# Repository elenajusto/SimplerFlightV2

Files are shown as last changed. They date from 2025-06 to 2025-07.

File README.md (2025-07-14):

# SimplerFlightV2

## Architecture
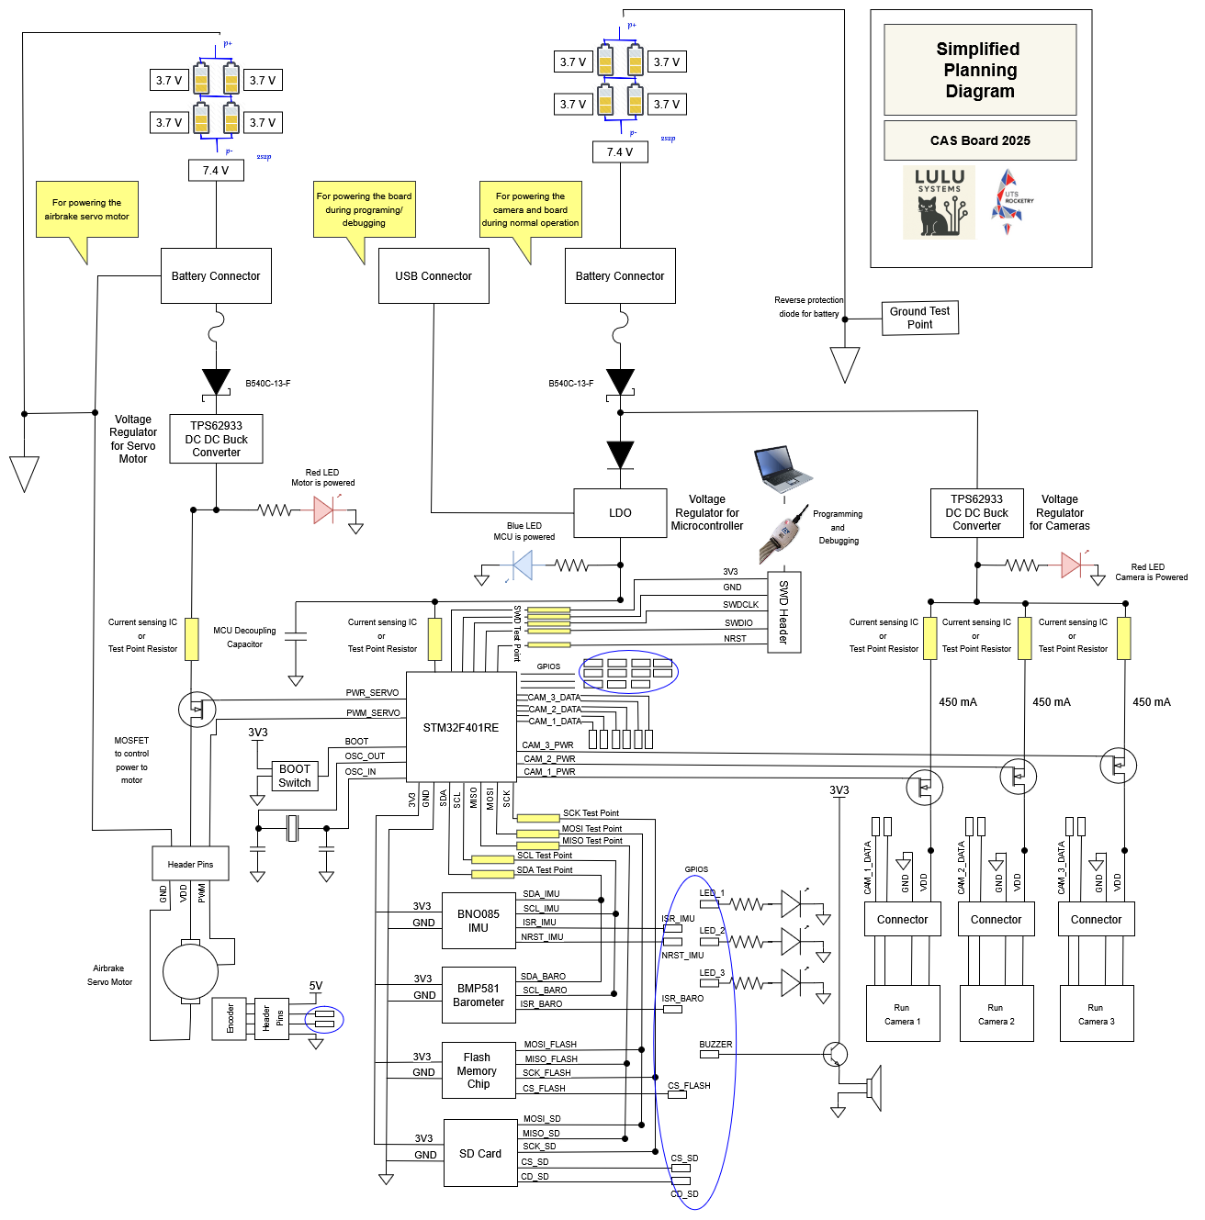
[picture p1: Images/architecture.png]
Architecture


## Simulations
Simulations done using Falstad. Available at: https://www.falstad.com/circuit/

### Buzzer
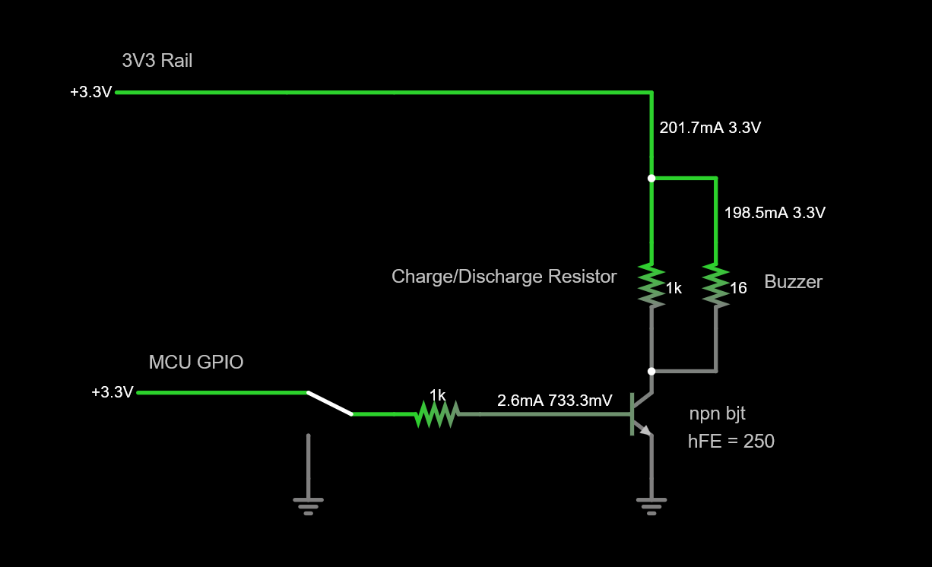
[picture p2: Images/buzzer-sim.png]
Buzzer-Sim


hFE value of 250 

As per characteristics of FSB560A NPN BJT at https://www.digikey.com/en/products/detail/onsemi/FSB560A/1049460

### Camera Power
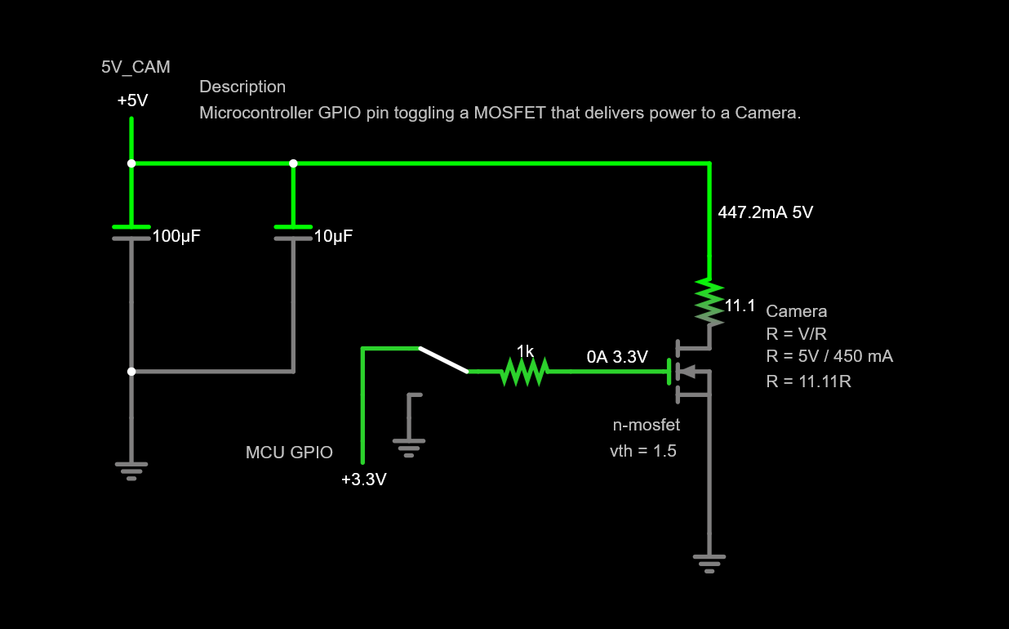
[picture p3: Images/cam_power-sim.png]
cam_power-sim-Sim


Beta value of 7.8

Assuming:
- RDS(on) (Ω) (use typical value): 0.16
- VGS where measured (V): 2.5
- Threshold (V) (use typical value): 3.3

As per characteristics of BSS816NWH6327XTSA1 N-MOSFET at https://www.digikey.com.au/en/products/detail/infineon-technologies/BSS816NWH6327XTSA1/5959970

## Microcontroller Pinout
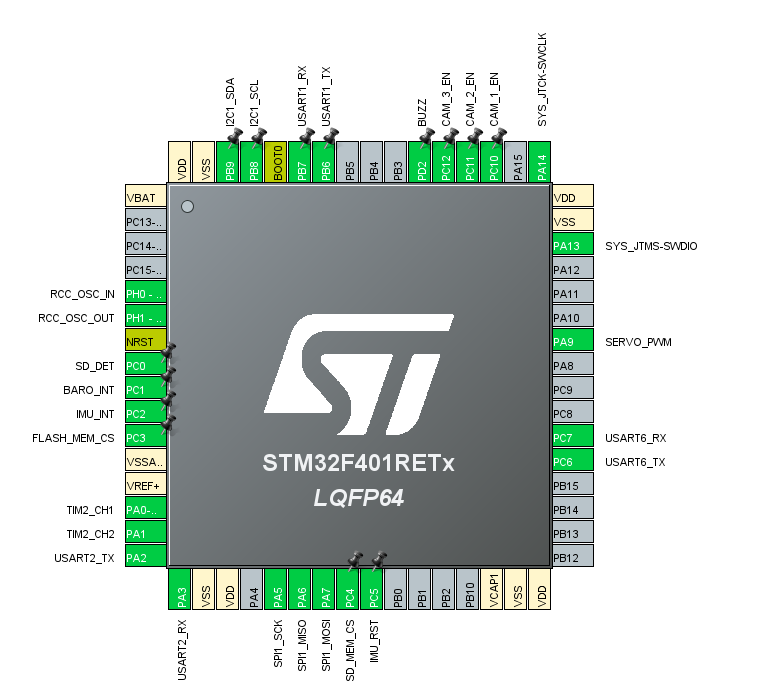
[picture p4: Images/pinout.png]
Pinout


## Schematic

### Root
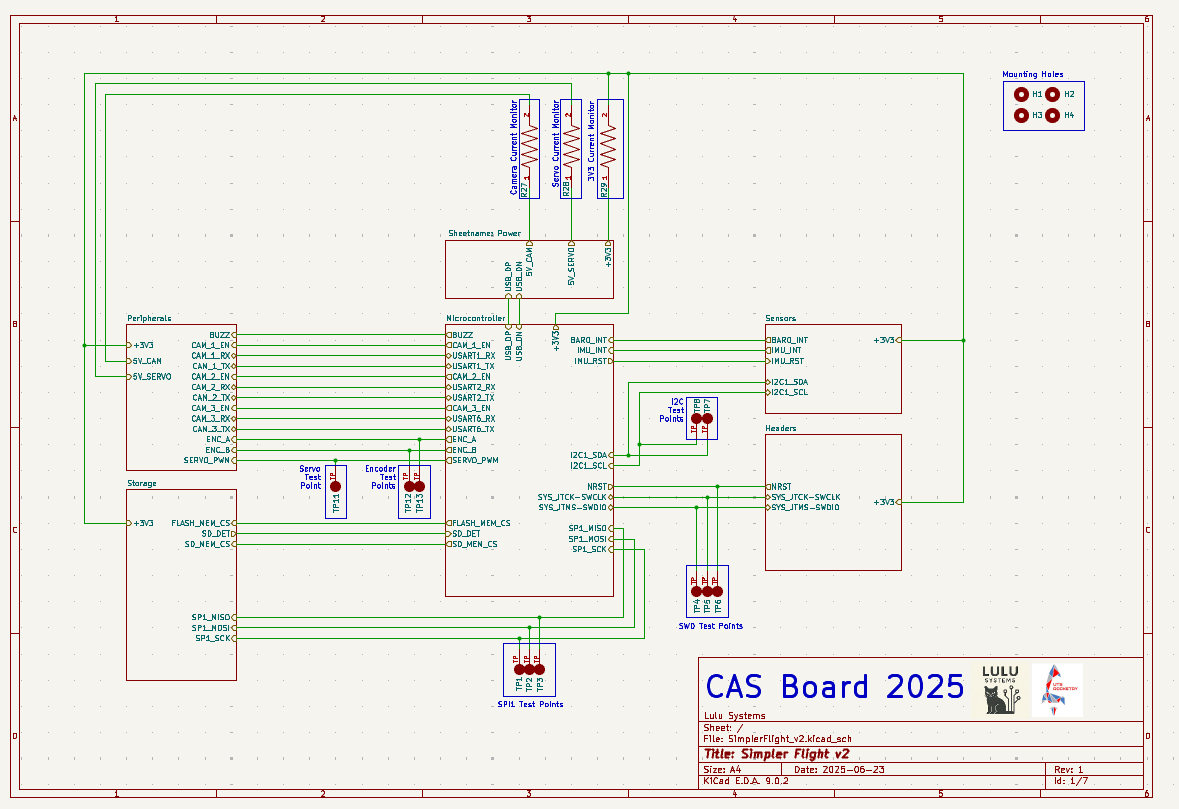
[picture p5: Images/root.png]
Root


### Microcontroller
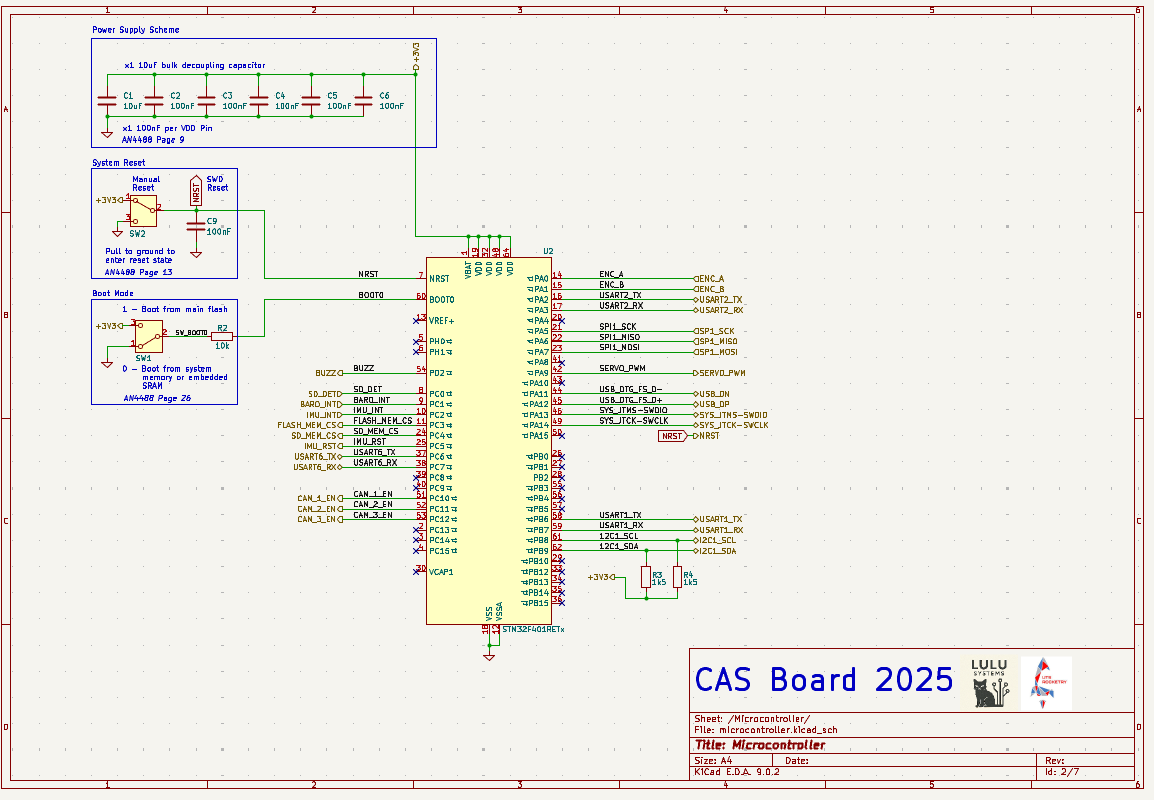
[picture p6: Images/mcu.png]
Microcontroller


### Power
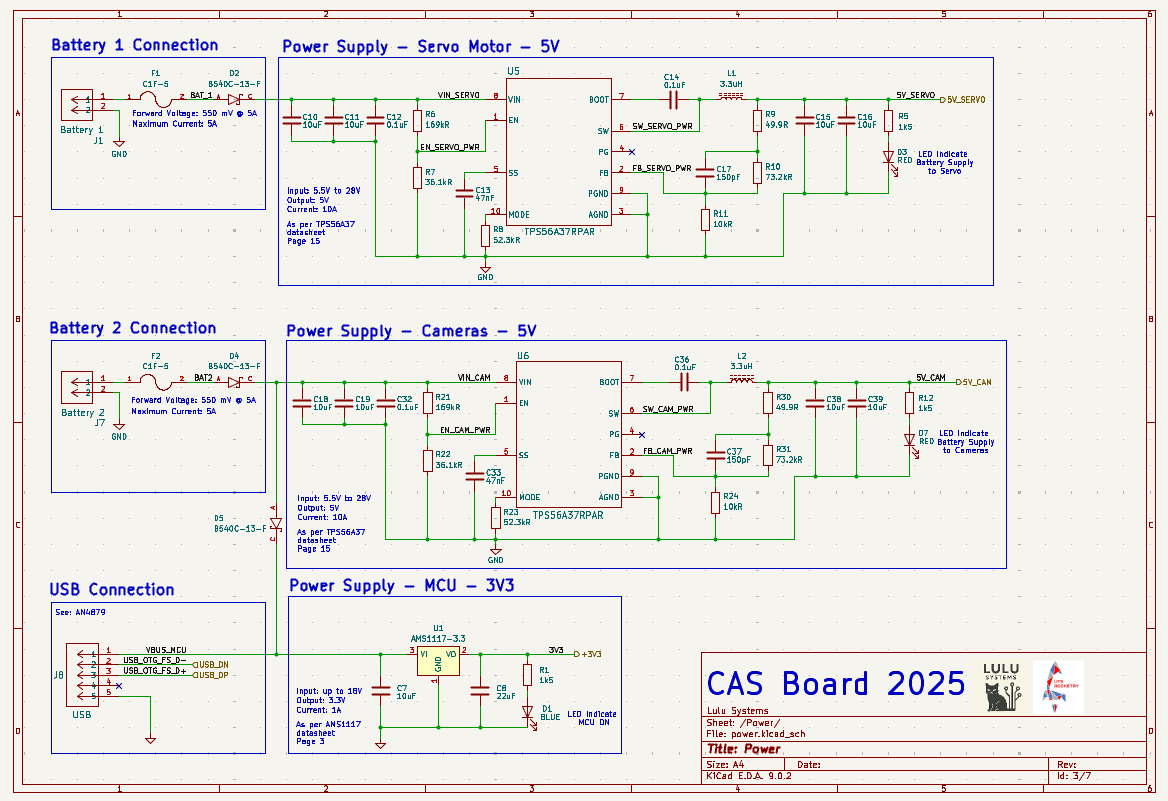
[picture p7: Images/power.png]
Power


### Sensors
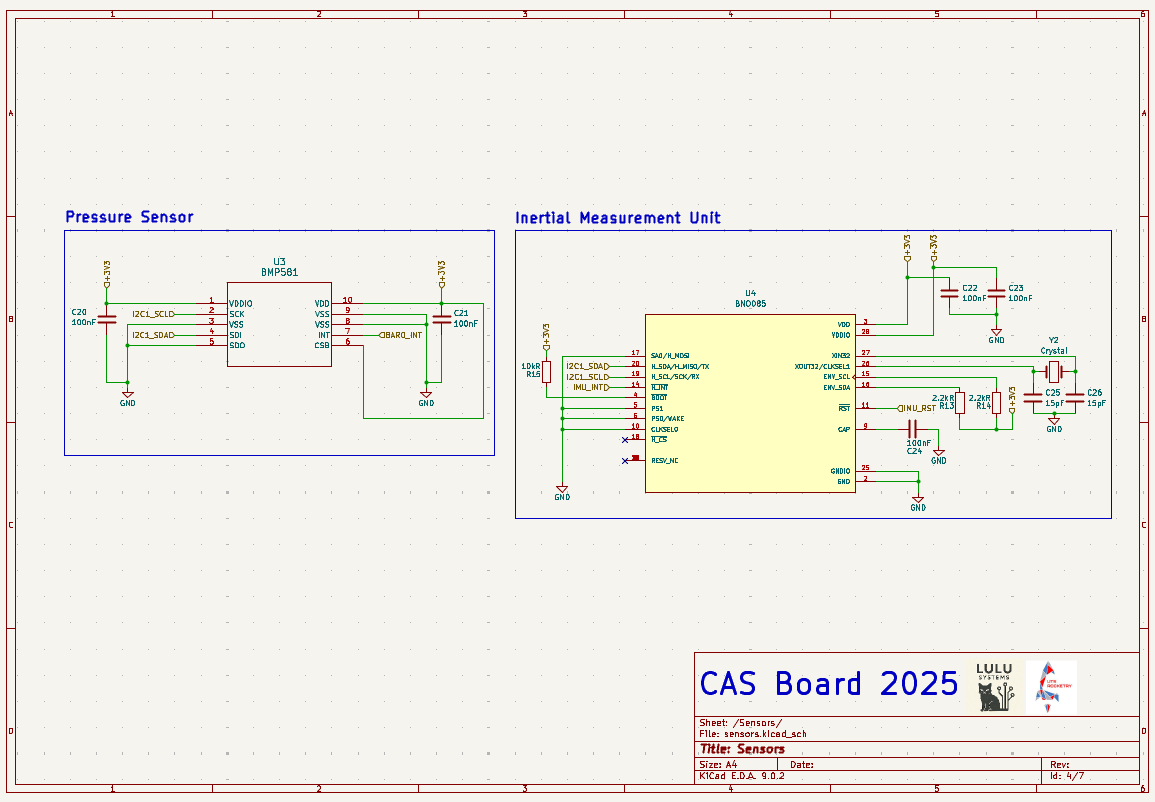
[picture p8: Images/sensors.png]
Sensors


### Storage
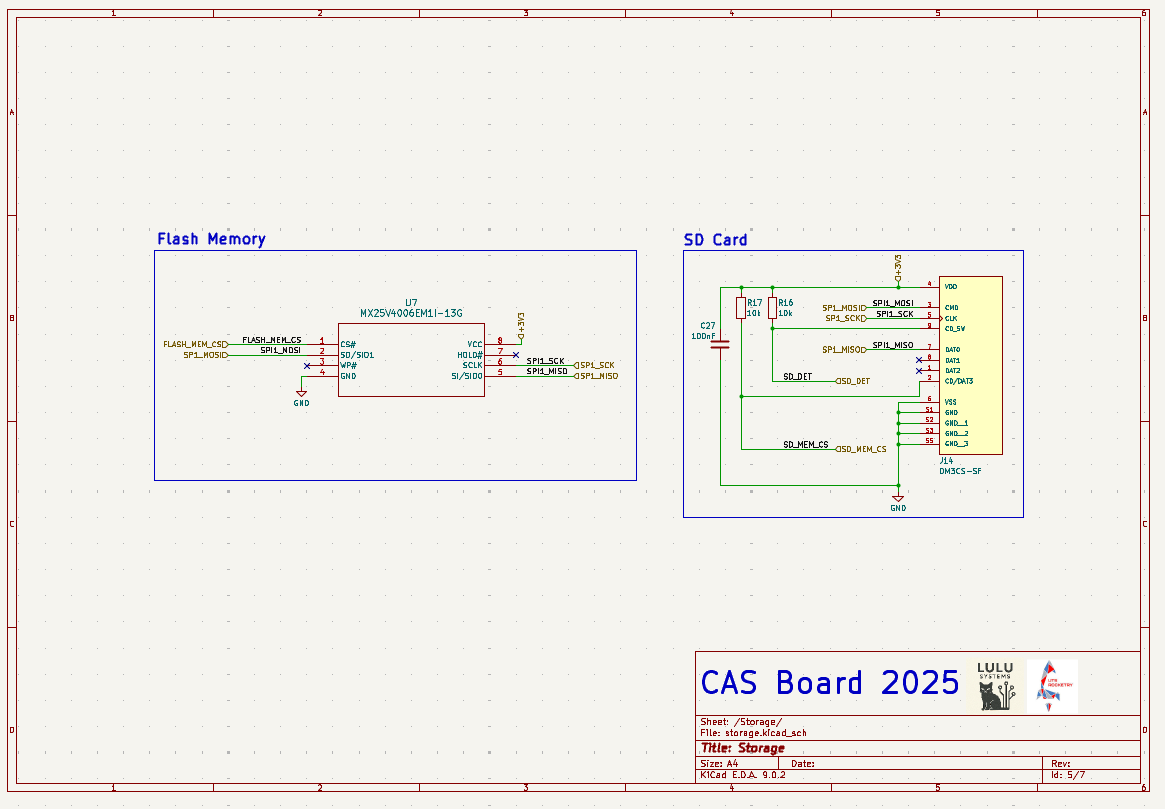
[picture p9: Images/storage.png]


### Peripherals
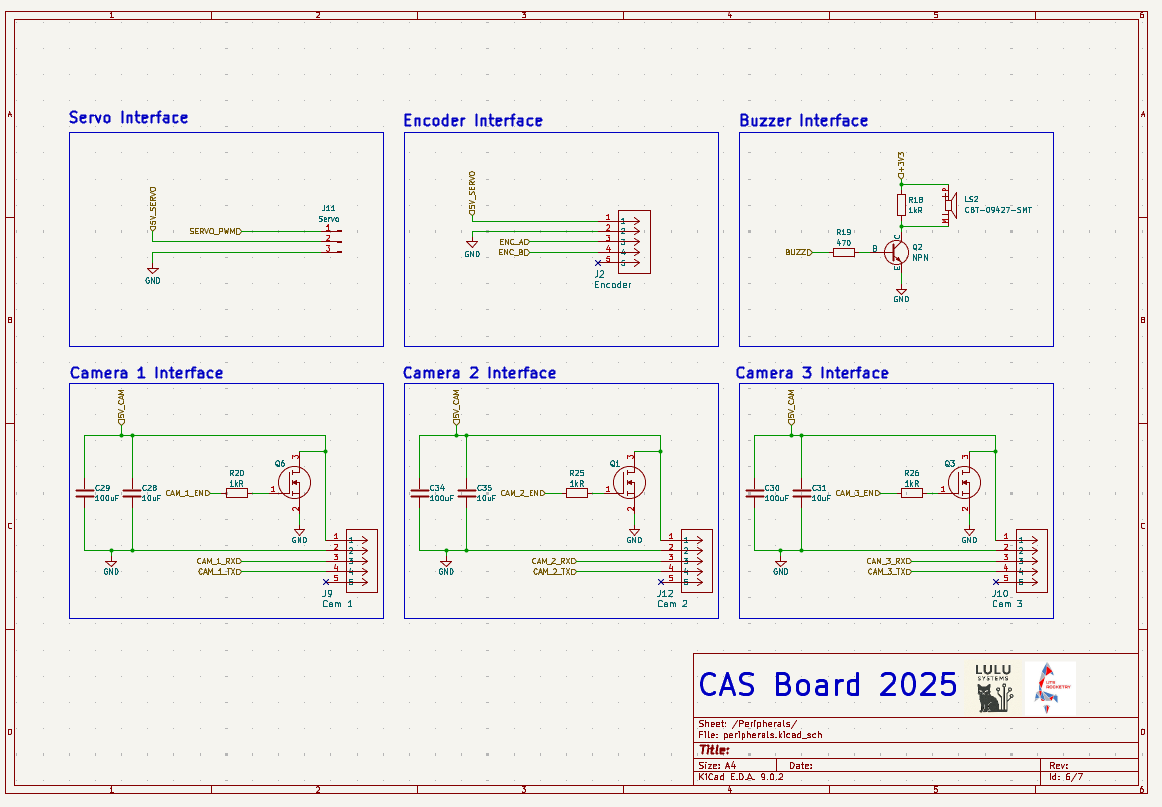
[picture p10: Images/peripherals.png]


### Headers
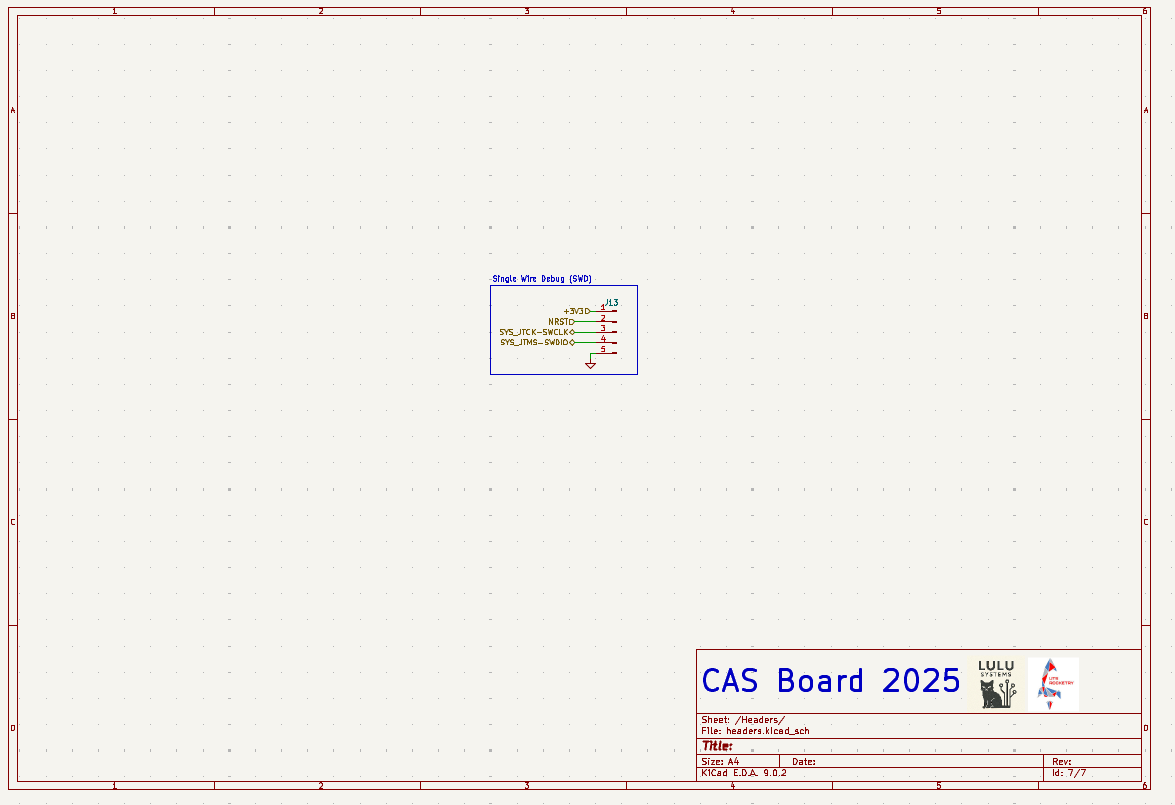
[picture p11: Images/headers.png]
Headers


## Routing
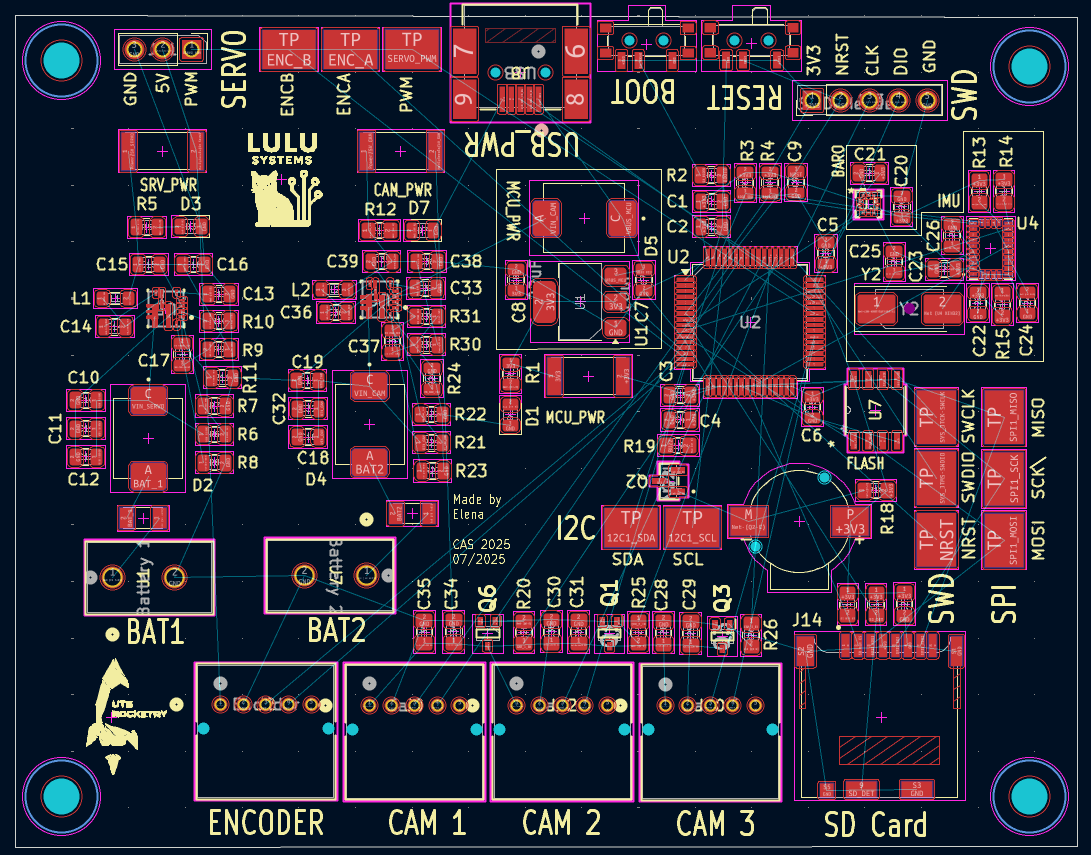
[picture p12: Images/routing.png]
Routing


## PCB
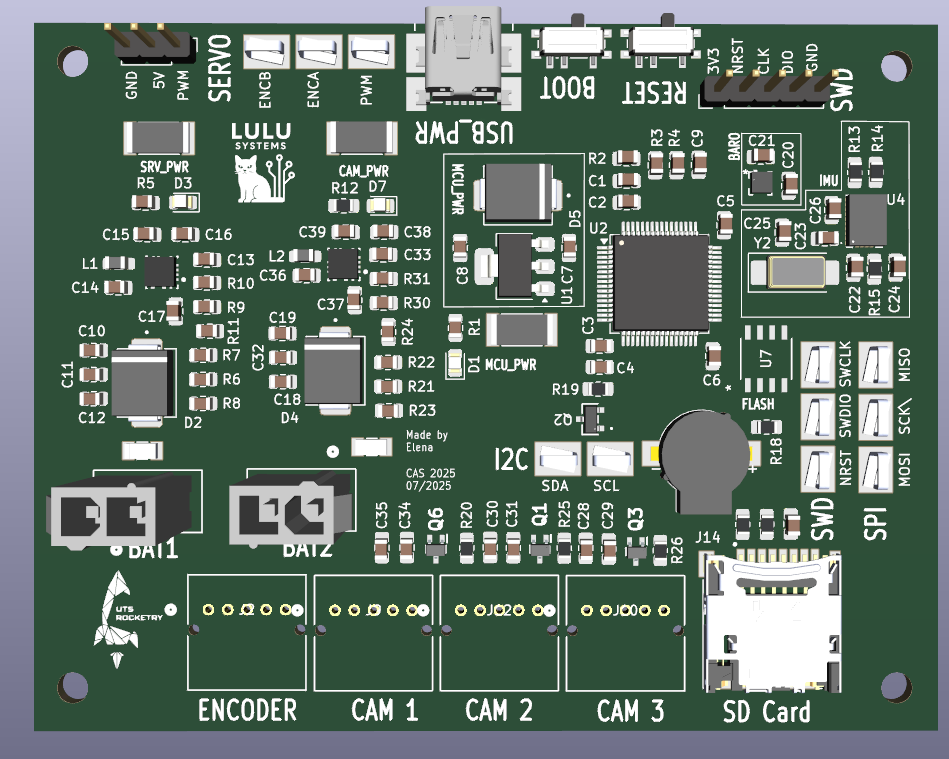
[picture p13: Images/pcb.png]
PCB


## Dimensions
94mm x 74mm

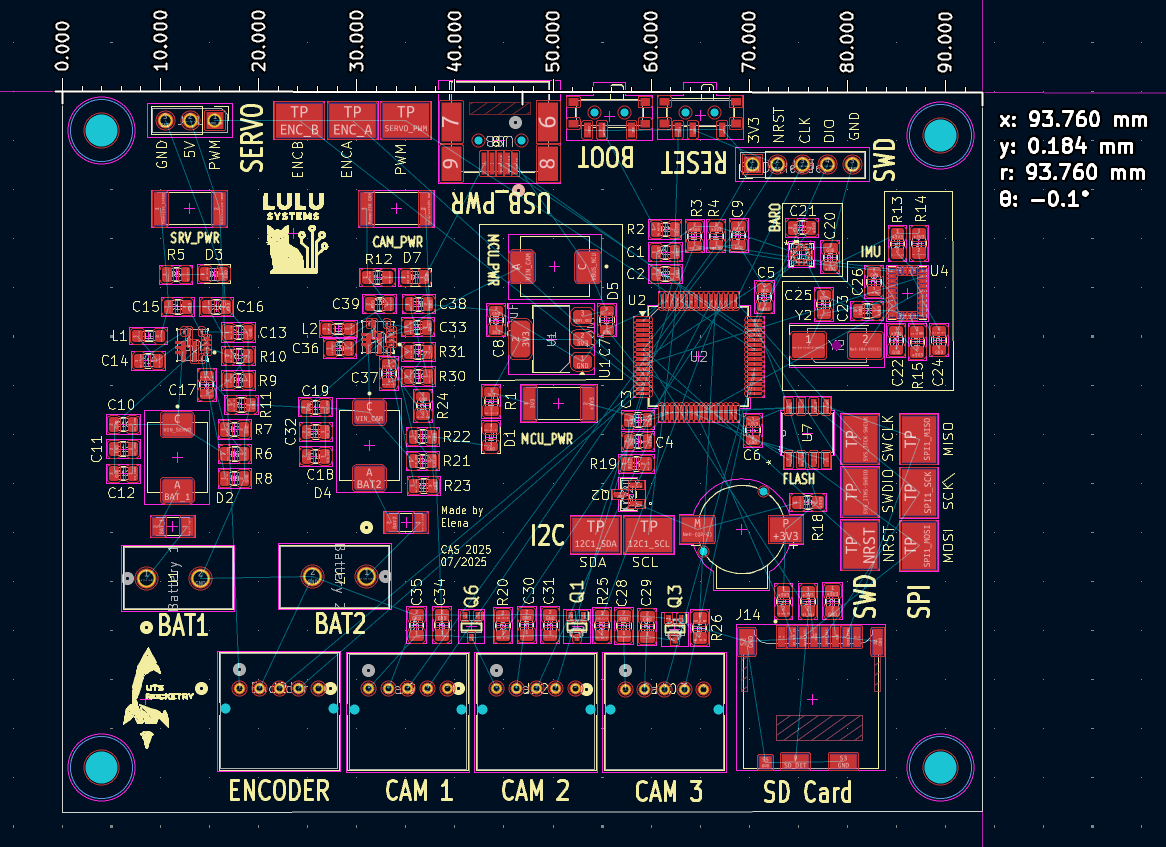
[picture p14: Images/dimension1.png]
Dimension 1


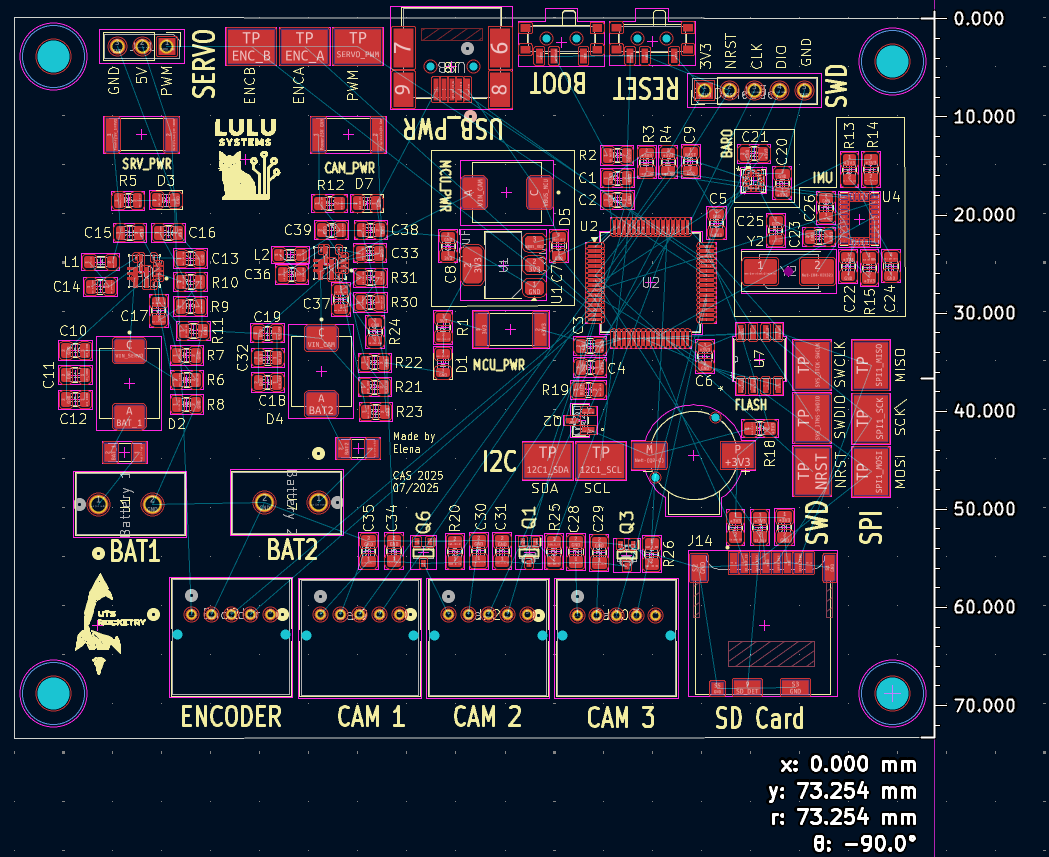
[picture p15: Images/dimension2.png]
Dimension 2


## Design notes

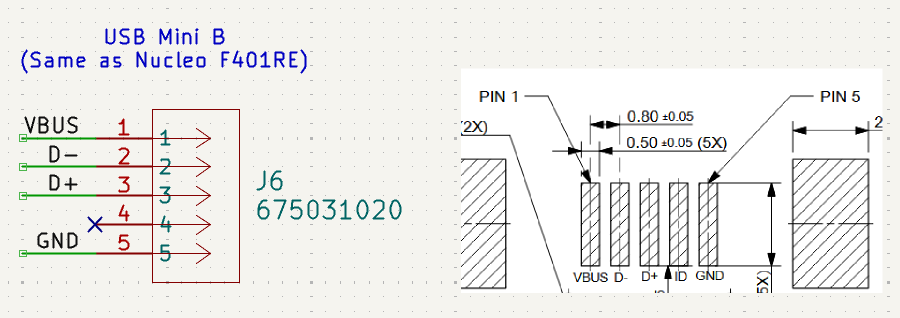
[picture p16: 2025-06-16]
Images/usb.png

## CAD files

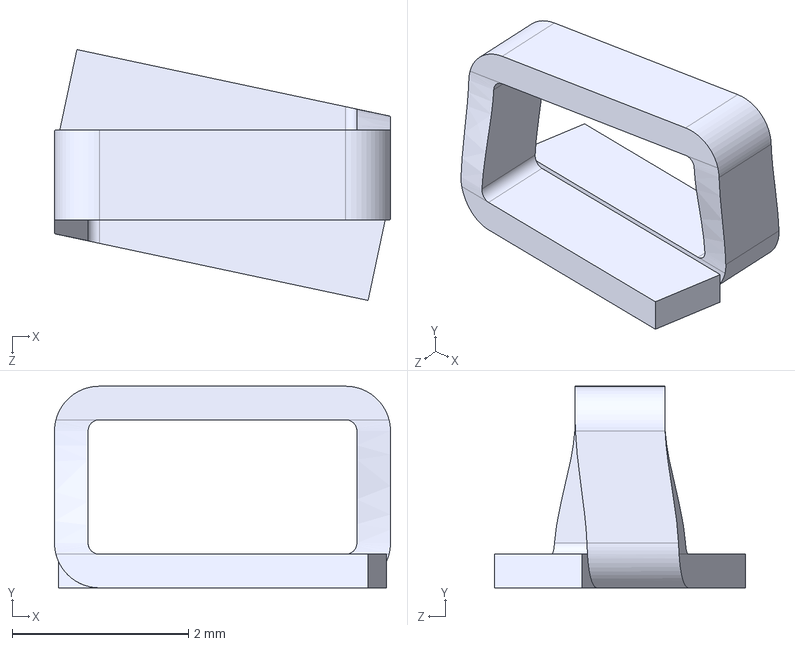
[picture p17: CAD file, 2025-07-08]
Components/5016/5016.step
3.81 x 2.29 x 2.84 mm

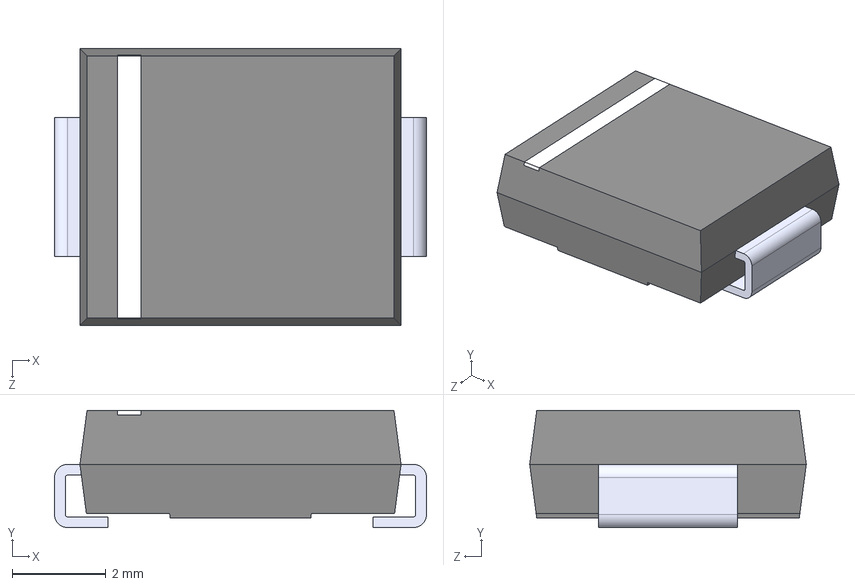
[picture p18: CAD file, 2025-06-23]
Components/B540C_13_F/B540C-13-F.step
7.94 x 2.50 x 5.91 mm

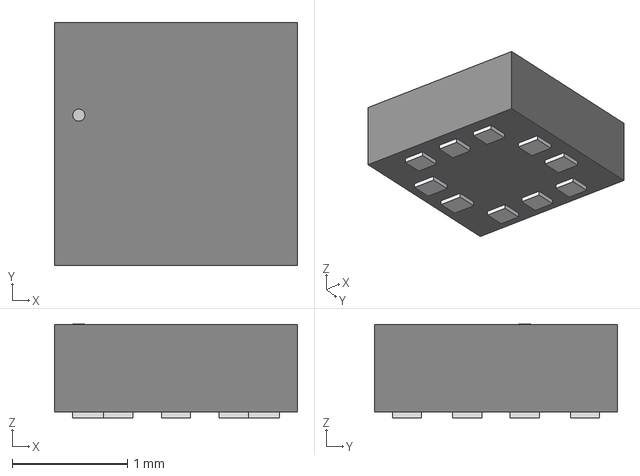
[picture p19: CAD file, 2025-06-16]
Components/BMP581/QFN10_BMP581_BOS.step
2.11 x 2.11 x 0.815 mm

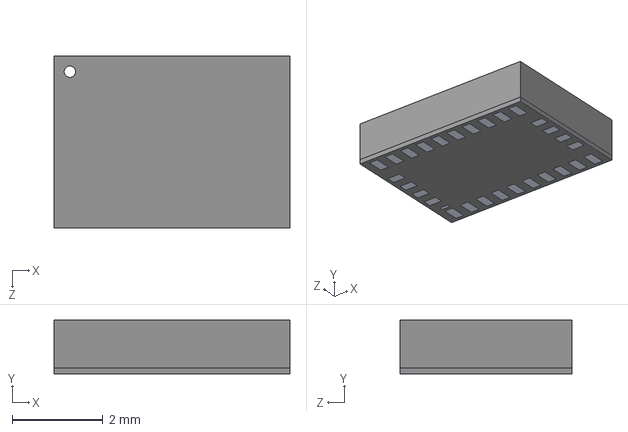
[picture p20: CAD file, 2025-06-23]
Components/BNO085/BNO085--3DModel-STEP-510211.STEP
5.20 x 1.18 x 3.80 mm

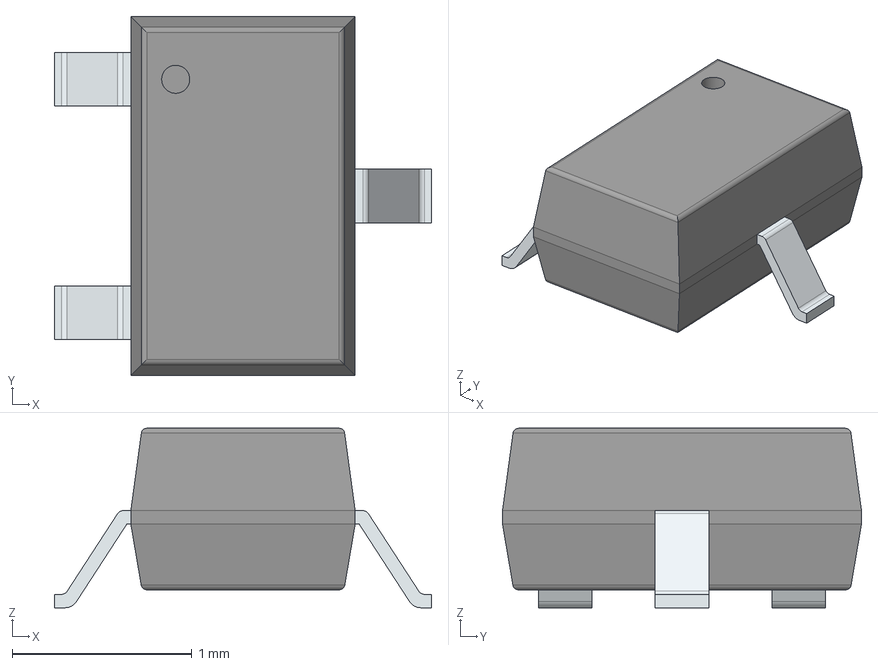
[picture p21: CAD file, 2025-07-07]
Components/BSS816NWH6327XTSA1/BSS816NWH6327XTSA1.stp
2.10 x 2.00 x 1.00 mm
PinsArrayL
FilletPinR

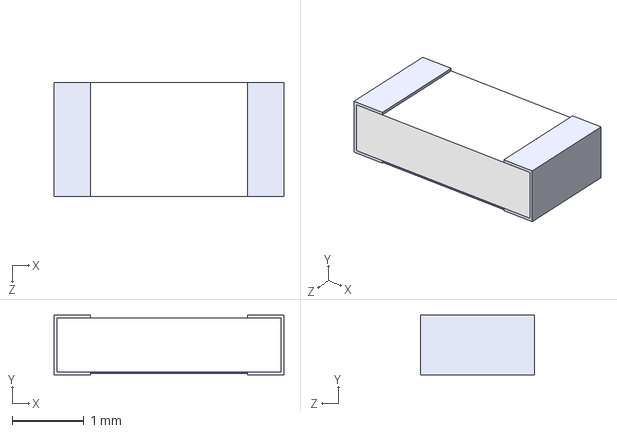
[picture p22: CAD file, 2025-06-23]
Components/C1F_5/C1F-5.step
3.20 x 0.83 x 1.58 mm

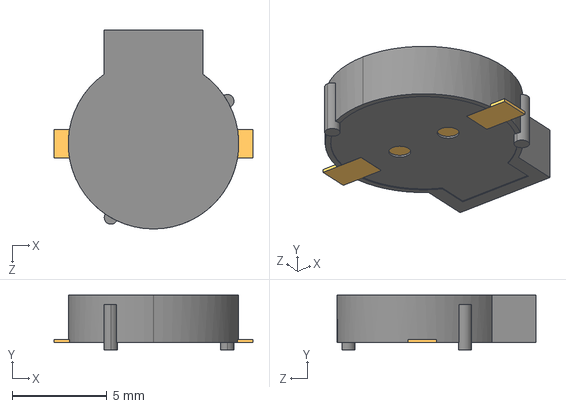
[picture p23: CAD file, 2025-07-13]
Components/CBT_09427_SMT_TR/CBT-09427-SMT.step
10.5 x 2.90 x 10.5 mm

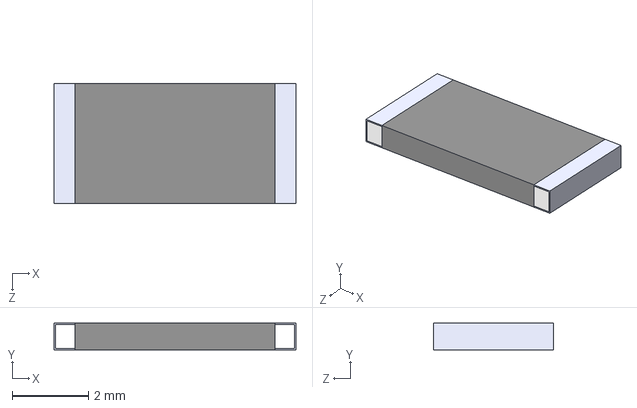
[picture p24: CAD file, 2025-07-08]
Components/CSRN2512FKR500/CSRN2512FKR500.step
6.35 x 0.7 x 3.15 mm

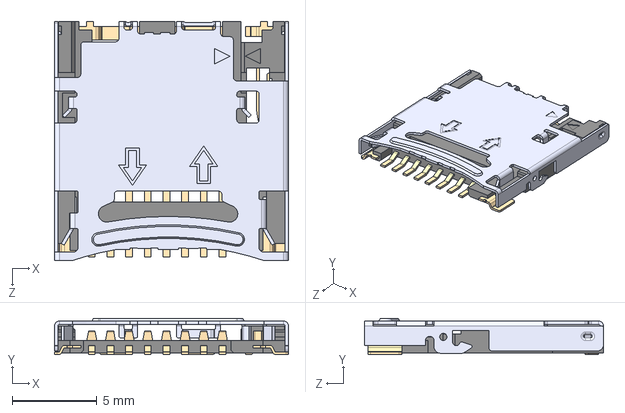
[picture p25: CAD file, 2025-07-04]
Components/DM3CS_SF/DM3CS-SF.step
13.8 x 2.13 x 14.1 mm

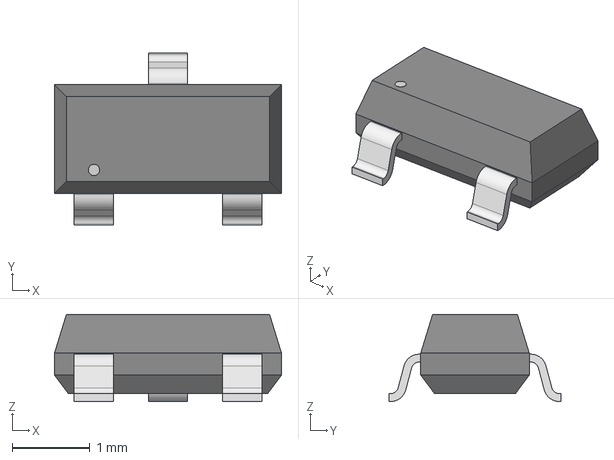
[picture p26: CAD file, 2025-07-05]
Components/FSB560A/SSOT3_3X1P5_ONS.step
2.92 x 2.21 x 1.12 mm

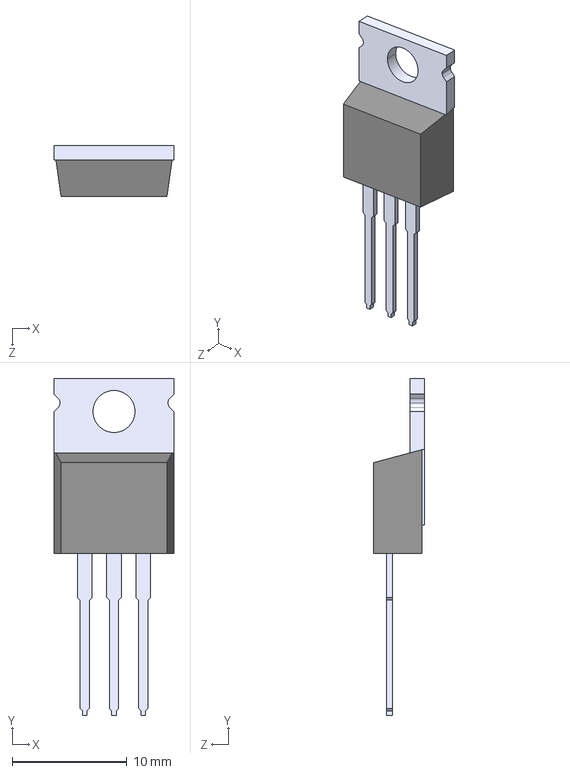
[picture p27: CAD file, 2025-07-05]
Components/IRF520NPBF/IRF520NPBF.step
10.4 x 29.3 x 4.45 mm

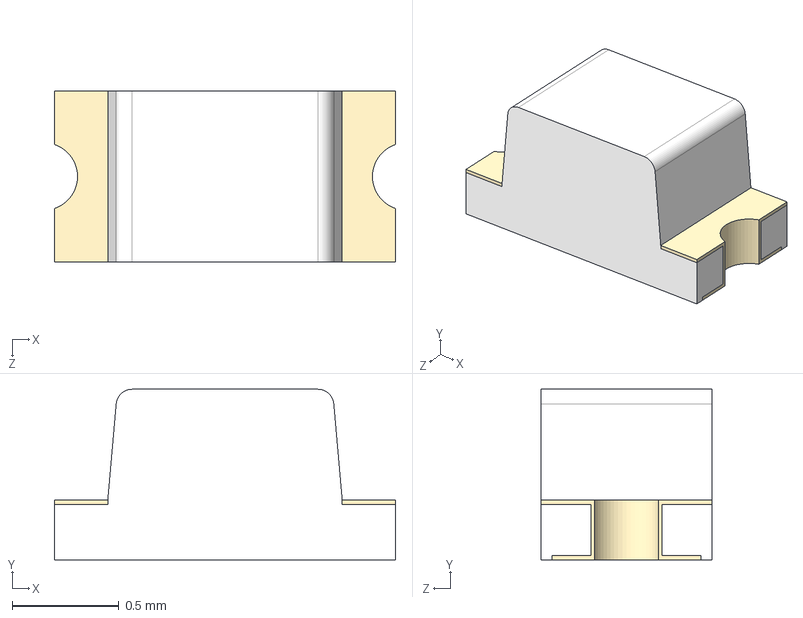
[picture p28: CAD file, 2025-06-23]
Components/LTST_C190KRKT/LTST-C190KRKT.step
1.60 x 0.8 x 0.8 mm

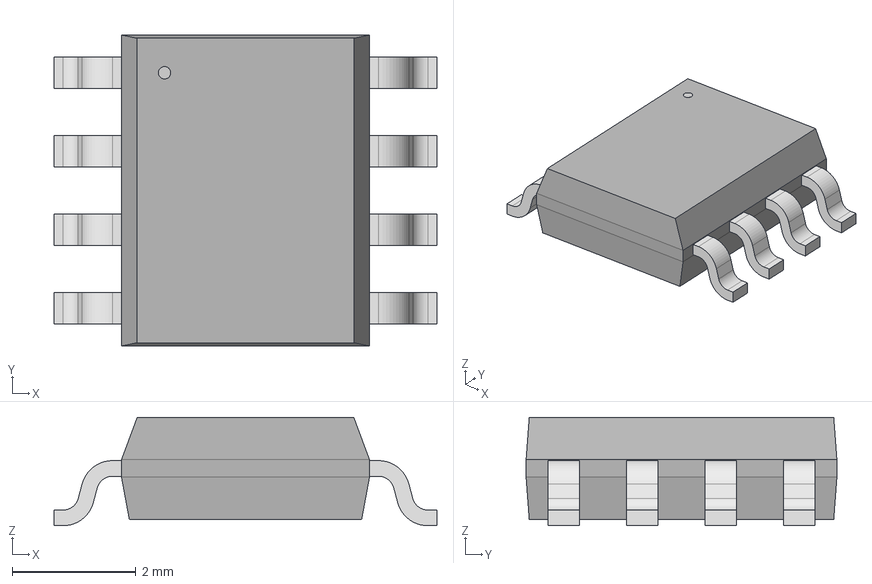
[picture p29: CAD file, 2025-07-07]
Components/MX25V4006EM1I_13G/SOP8_150_MAC.step
6.20 x 5.03 x 1.75 mm

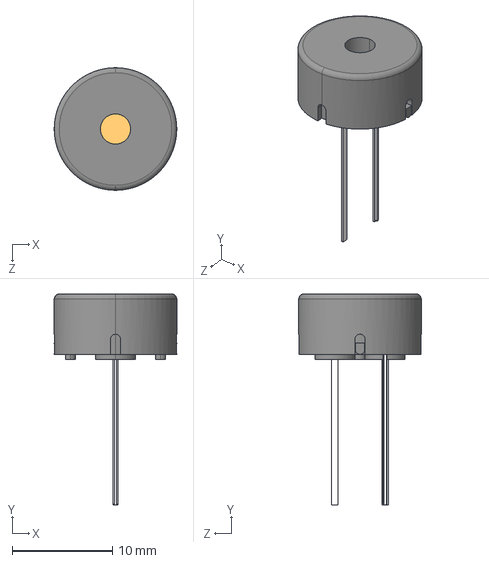
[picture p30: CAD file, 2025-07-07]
Components/PS1240P02BT/PS1240P02BT.step
12.2 x 21.0 x 12.2 mm

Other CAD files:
Components/TPS56A37RPAR/RPA0010A.stp
Components/W25X40CLSNIG/WIN_SN-8_WIN.step
Components/39281023/039281023.stp
Components/675031020/675031020.stp
Components/TPS62933DRLR/TPS62933DRLR.step

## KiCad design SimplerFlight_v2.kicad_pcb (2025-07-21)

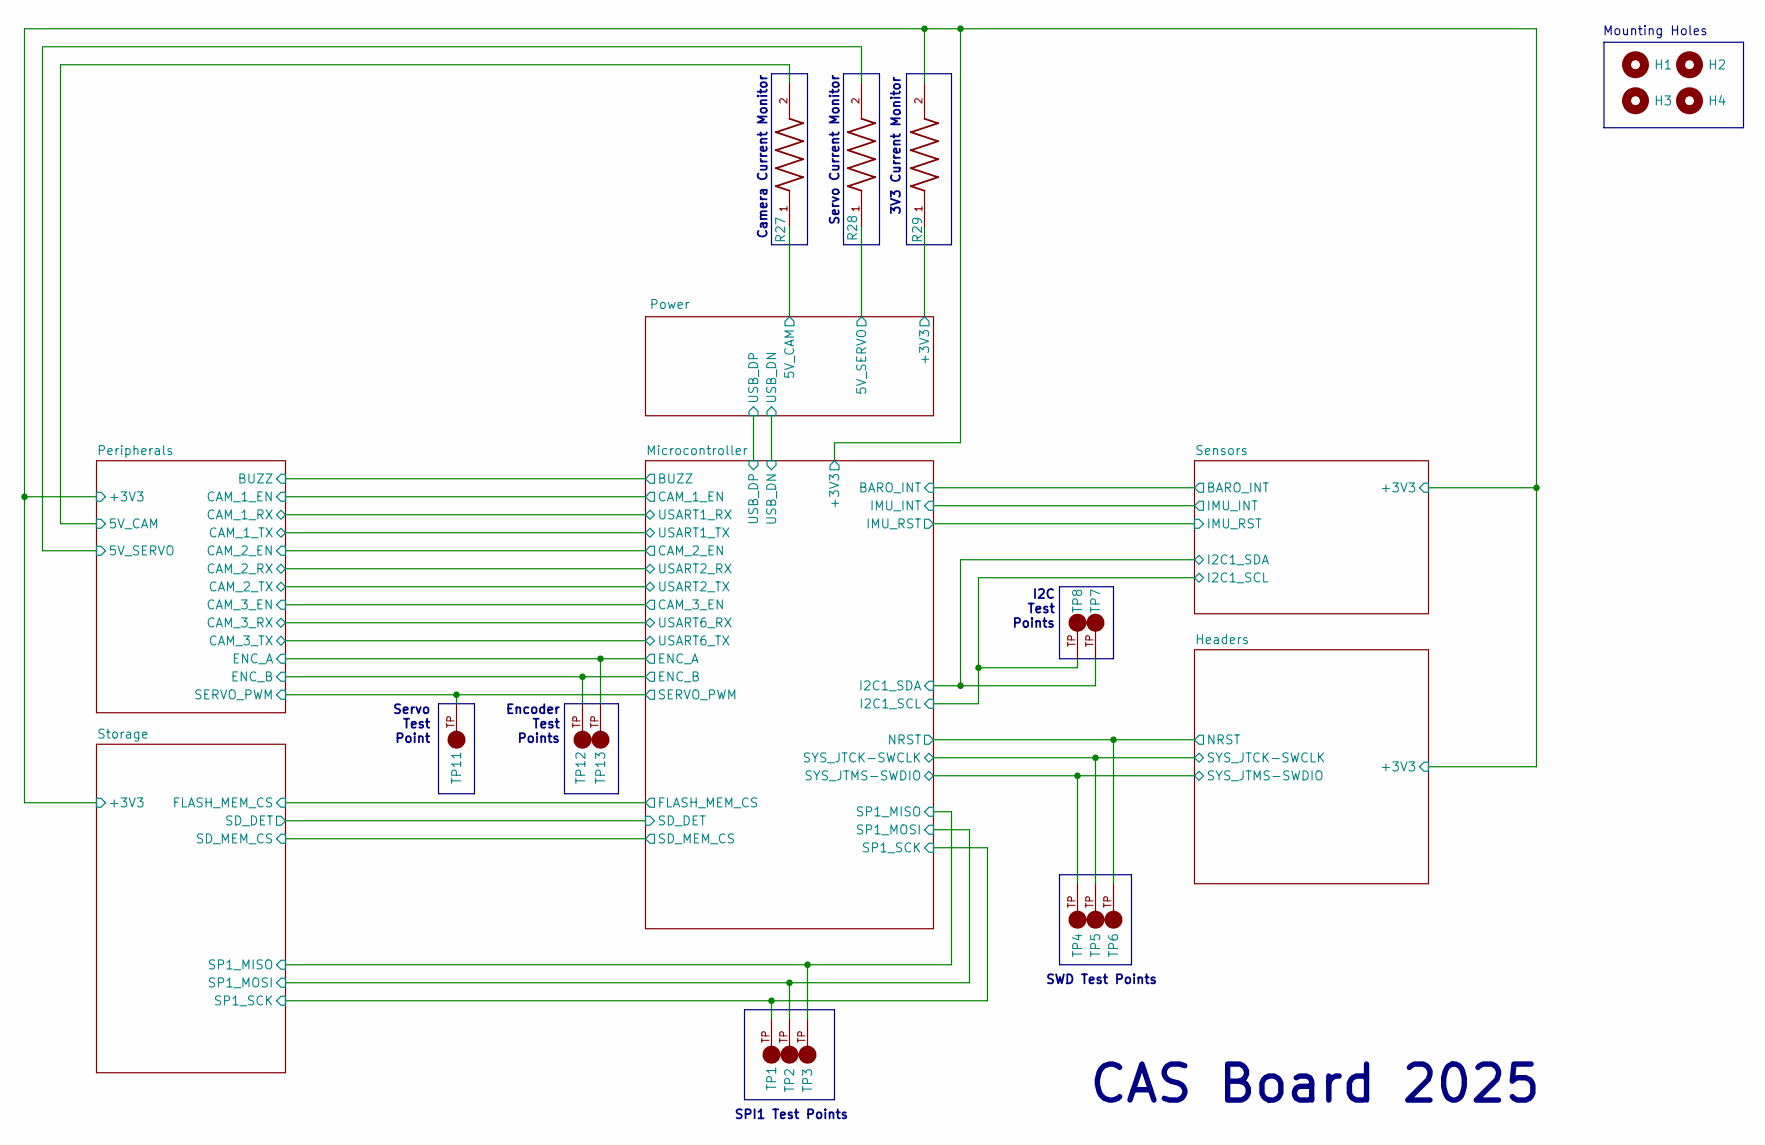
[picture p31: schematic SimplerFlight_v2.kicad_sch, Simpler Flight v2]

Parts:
H1, H2, H3, H4: MountingHole; MountingHole_3.2mm_M3
R27, R28, R29: CSRN2512FKR500; RESC6331X70N
TP1, TP2, TP3, TP4, TP5, TP6, TP7, TP8, TP11, TP12, TP13: 5016; KEYSTONE_5016; PARTREV D

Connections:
/Headers/+3V3: R29.2; also elsewhere on the board
/Peripherals/5V_CAM: R27.2; also elsewhere on the board
/Peripherals/5V_SERVO: R28.2; also elsewhere on the board
/Power/3V3: R29.1; also elsewhere on the board
/Power/5V_CAM: R27.1; also elsewhere on the board
/Power/5V_SERVO: R28.1; also elsewhere on the board

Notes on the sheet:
SWD Test Points
3V3 Current Monitor
I2C Test Points
Servo Test Point
SPI1 Test Points
Servo Current Monitor
CAS Board 2025
Mounting Holes
Camera Current Monitor
Encoder Test Points

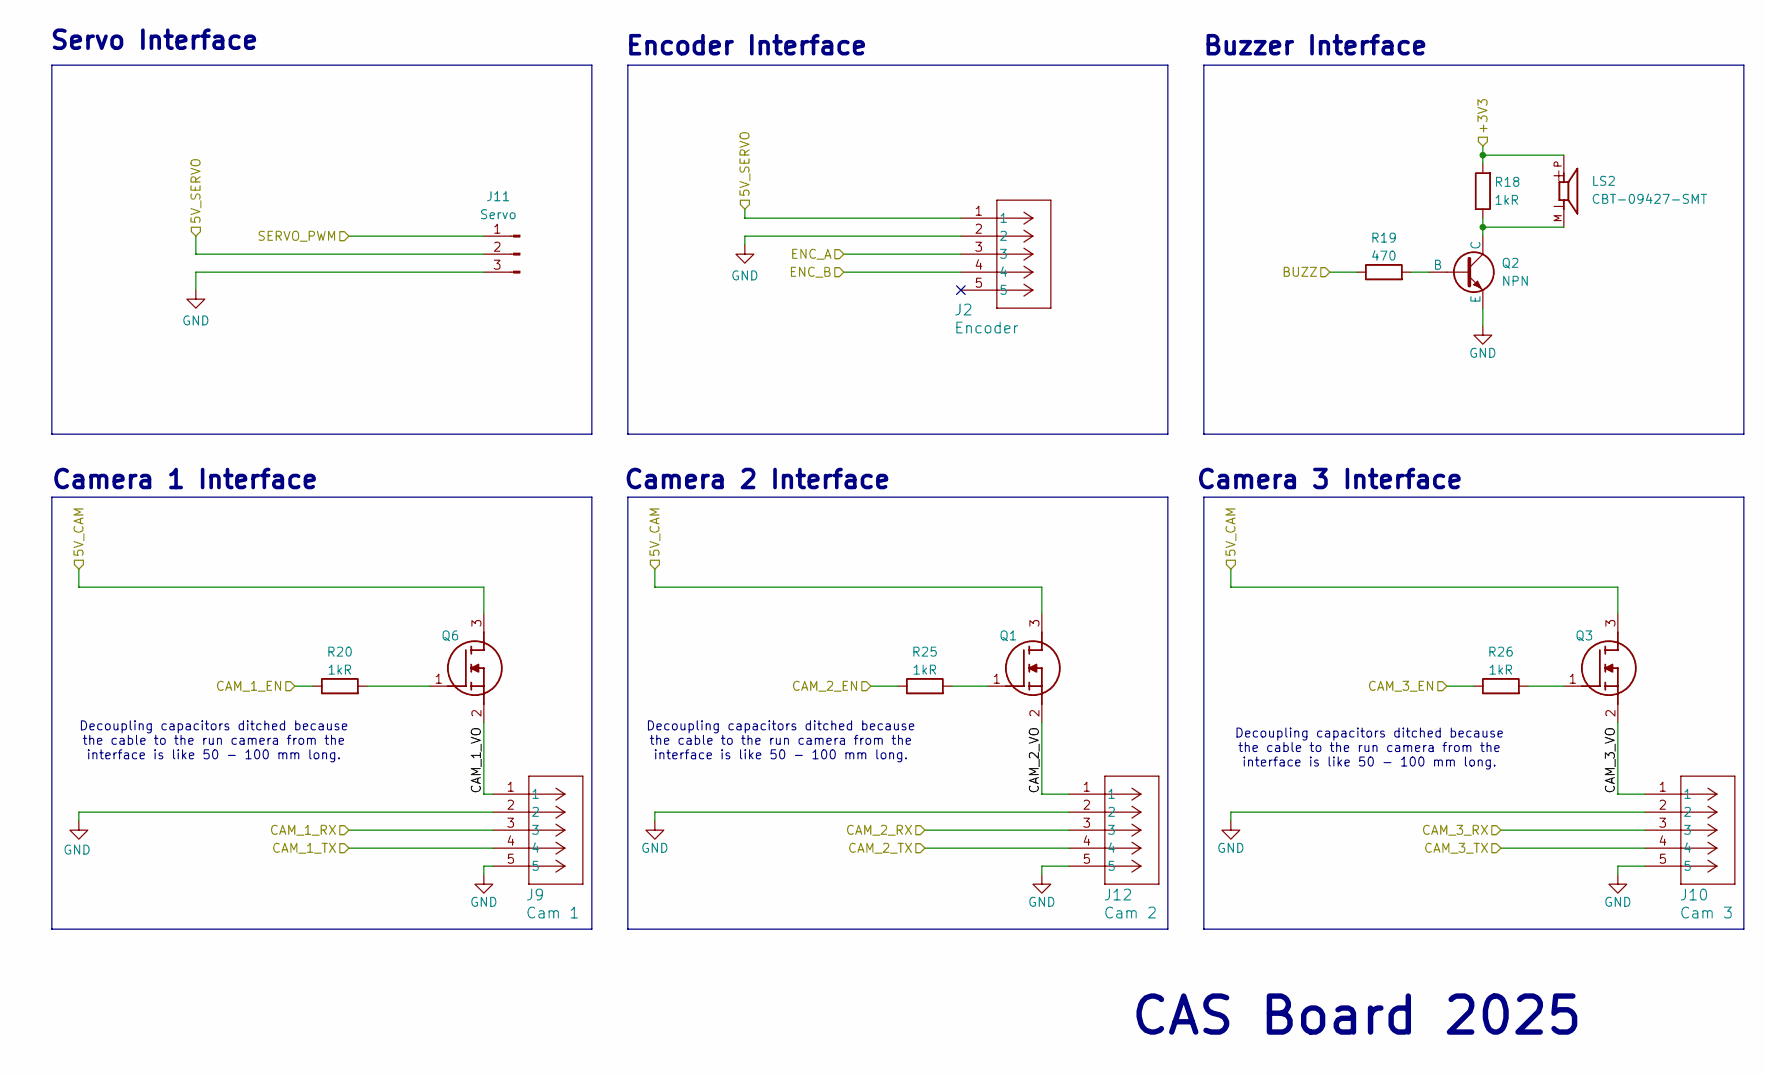
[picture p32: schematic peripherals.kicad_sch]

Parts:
J2: Encoder; CONN_S05B-PASK-2_JST
J9: Cam 1; CONN_S05B-PASK-2_JST
J10: Cam 3; CONN_S05B-PASK-2_JST
J11: Servo; PinHeader_1x03_P2.54mm_Vertical
J12: Cam 2; CONN_S05B-PASK-2_JST
LS2: CBT-09427-SMT; CUI_CBT-09427-SMT
Q1, Q3, Q6: BSS816NWH6327XTSA1; SOT65P210X100-3N; Mouser Part Number 726-SP000917562
Q2: NPN; SSOT3_3X1P5_ONS
R18, R20, R25, R26: 1kR; R_0805_2012Metric_Pad1.20x1.40mm_HandSolder
R19: 470; R_0805_2012Metric_Pad1.20x1.40mm_HandSolder

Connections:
/Headers/+3V3: LS2.P, R18.2; also elsewhere on the board
/Microcontroller/BUZZ: R19.1; also elsewhere on the board
/Microcontroller/CAM_1_EN: R20.1; also elsewhere on the board
/Microcontroller/CAM_2_EN: R25.1; also elsewhere on the board
/Microcontroller/CAM_3_EN: R26.1; also elsewhere on the board
/Microcontroller/ENC_A: J2.3; also elsewhere on the board
/Microcontroller/ENC_B: J2.4; also elsewhere on the board
/Microcontroller/SERVO_PWM: J11.1; also elsewhere on the board
/Microcontroller/USART1_RX: J9.3; also elsewhere on the board
/Microcontroller/USART1_TX: J9.4; also elsewhere on the board
/Microcontroller/USART2_RX: J12.3; also elsewhere on the board
/Microcontroller/USART2_TX: J12.4; also elsewhere on the board
/Microcontroller/USART6_RX: J10.3; also elsewhere on the board
/Microcontroller/USART6_TX: J10.4; also elsewhere on the board
/Peripherals/5V_CAM: Q1.3 (D), Q3.3 (D), Q6.3 (D); also elsewhere on the board
/Peripherals/5V_SERVO: J2.1, J11.2; also elsewhere on the board
/Peripherals/CAM_1_VO: J9.1, Q6.2 (S)
/Peripherals/CAM_2_VO: J12.1, Q1.2 (S)
/Peripherals/CAM_3_VO: J10.1, Q3.2 (S)
GND: J2.2, J9.2, J9.5, J10.2, J10.5, J11.3, J12.2, J12.5, Q2.3 (E); also elsewhere on the board
unnamed: Q1.1 (G), R25.2
unnamed: Q2.2 (B), R19.2
unnamed: LS2.M, Q2.1 (C), R18.1
unnamed: Q3.1 (G), R26.2
unnamed: Q6.1 (G), R20.2

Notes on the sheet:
Decoupling capacitors ditched because the cable to the run camera from the interface is like 50 - 100 mm long.
Camera 1 Interface
Encoder Interface
CAS Board 2025
Camera 3 Interface
Camera 2 Interface
Servo Interface
Buzzer Interface

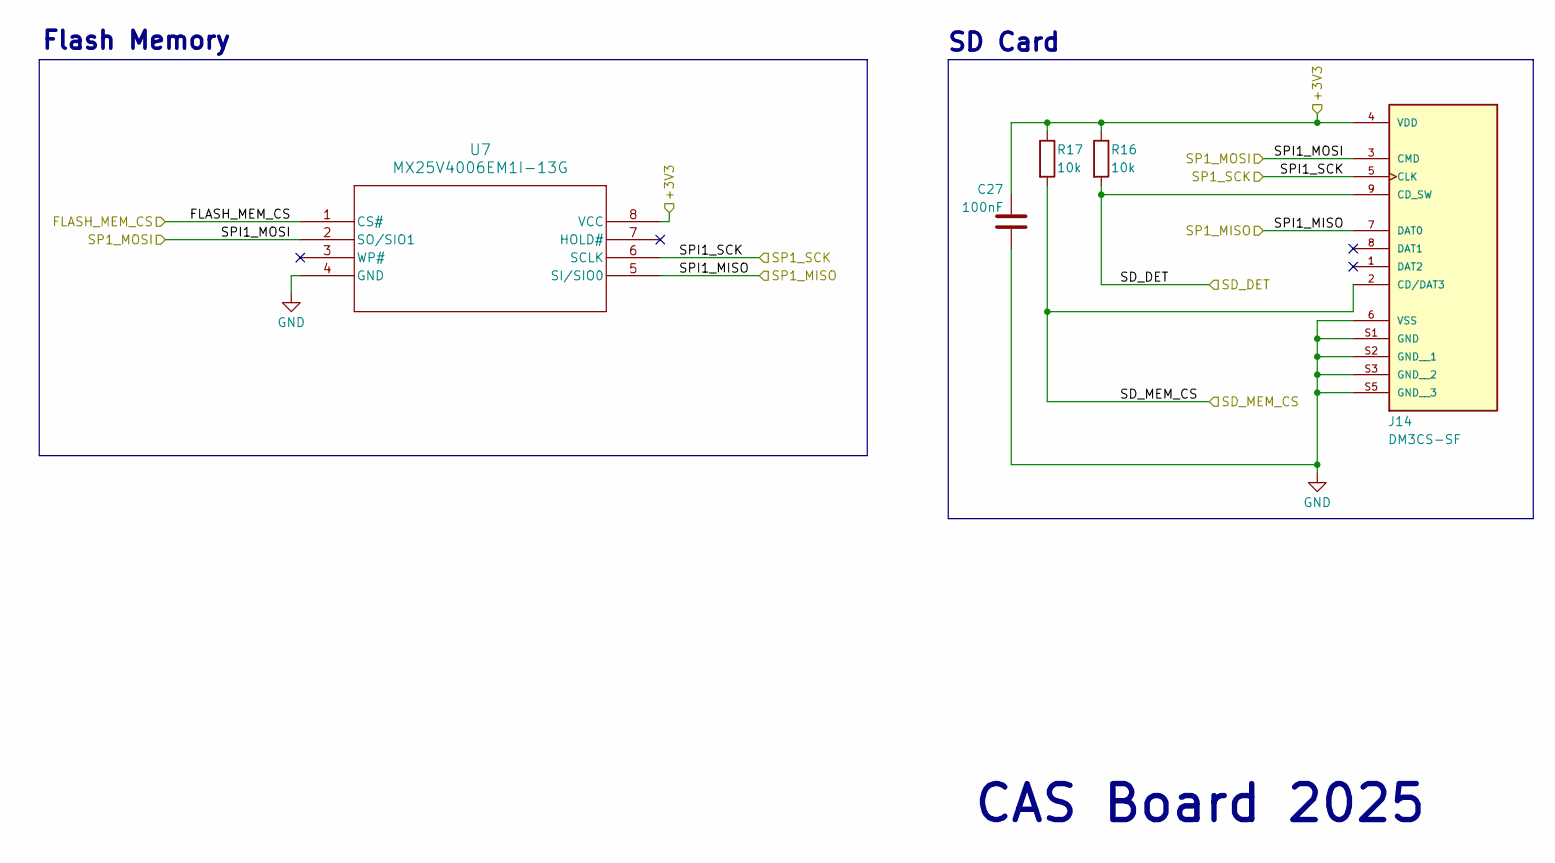
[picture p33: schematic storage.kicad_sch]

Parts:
C27: 100nF; C_0805_2012Metric_Pad1.18x1.45mm_HandSolder
J14: DM3CS-SF; HRS_DM3CS-SF; PARTREV n/a
R16, R17: 10k; R_0805_2012Metric_Pad1.20x1.40mm_HandSolder
U7: MX25V4006EM1I-13G; SOP8_150_MAC

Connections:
/Headers/+3V3: C27.1, J14.4 (VDD), R16.1, R17.1, U7.8 (VCC); also elsewhere on the board
/Microcontroller/FLASH_MEM_CS: U7.1 (CS#); also elsewhere on the board
/Microcontroller/SD_DET: J14.9 (CD_SW), R16.2; also elsewhere on the board
/Microcontroller/SD_MEM_CS: J14.2 (CD/DAT3), R17.2; also elsewhere on the board
/Microcontroller/SPI1_MISO: J14.7 (DAT0), U7.5 (SI/SIO0); also elsewhere on the board
/Microcontroller/SPI1_MOSI: J14.3 (CMD), U7.2 (SO/SIO1); also elsewhere on the board
/Microcontroller/SPI1_SCK: J14.5 (CLK), U7.6 (SCLK); also elsewhere on the board
GND: C27.2, J14.6 (VSS), J14.S1 (GND), J14.S2 (GND__1), J14.S3 (GND__2), J14.S5 (GND__3), U7.4 (GND); also elsewhere on the board

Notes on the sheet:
Flash Memory
SD Card
CAS Board 2025

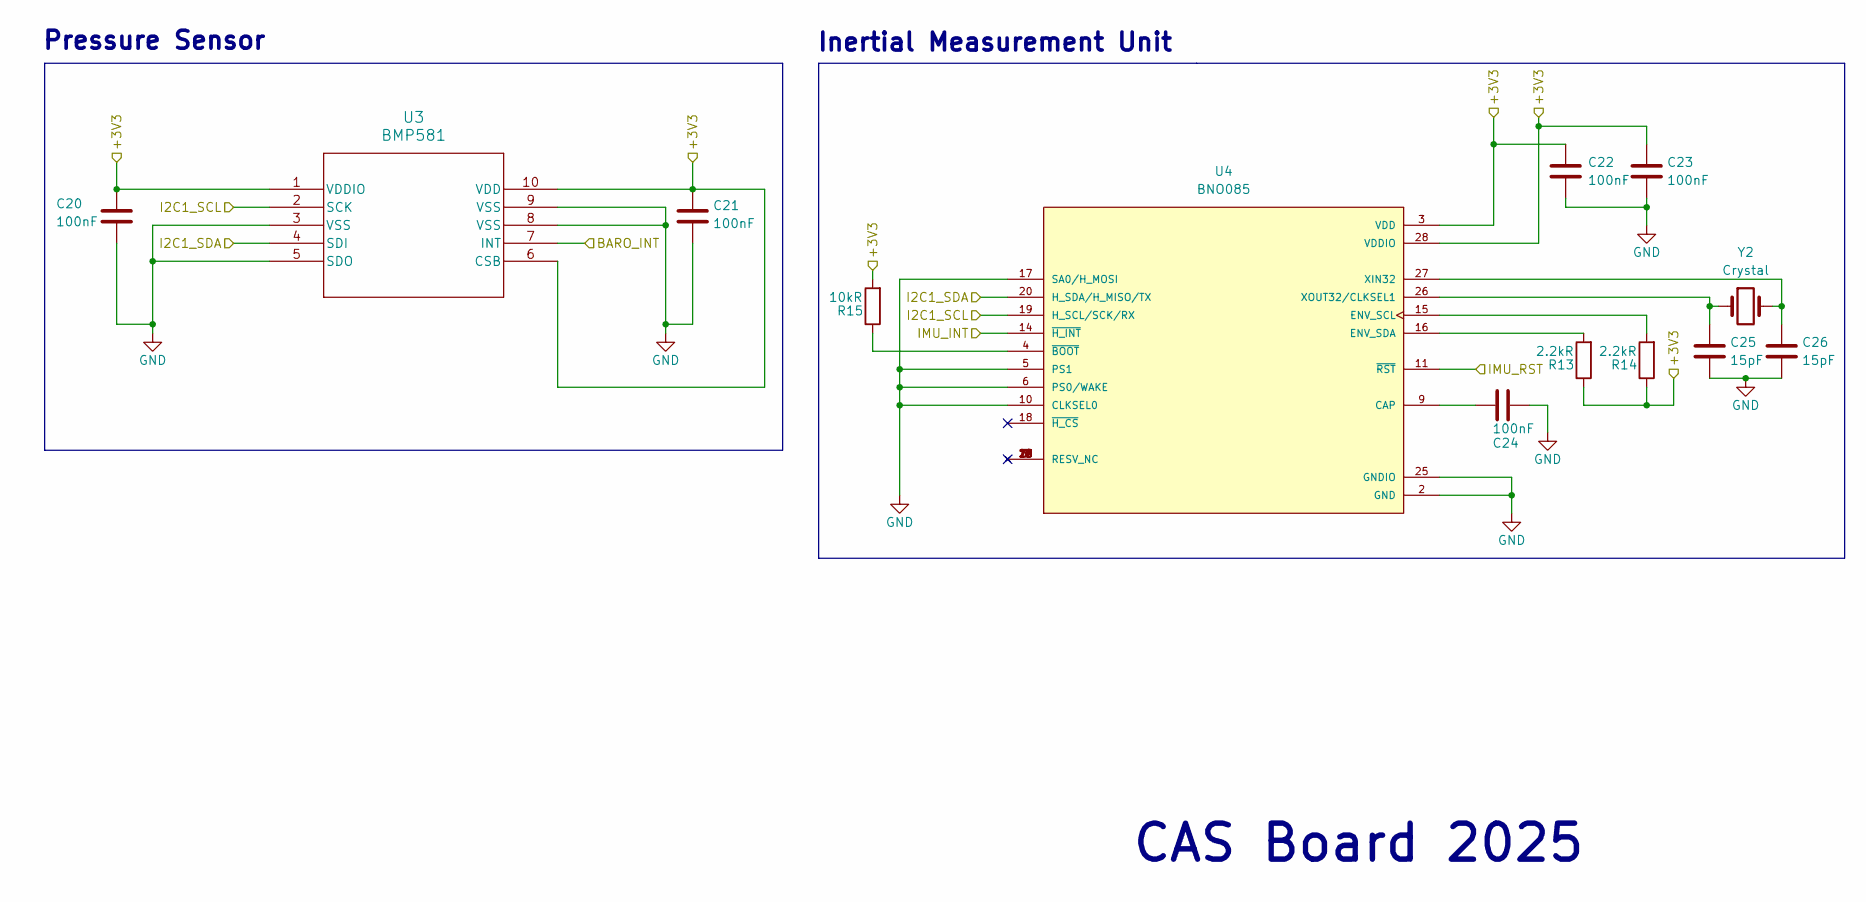
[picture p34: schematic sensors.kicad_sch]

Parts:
C20, C21, C22, C23, C24: 100nF; C_0805_2012Metric
C25, C26: 15pF; C_0805_2012Metric
R13, R14: 2.2kR; R_0805_2012Metric_Pad1.20x1.40mm_HandSolder
R15: 10kR; R_0805_2012Metric_Pad1.20x1.40mm_HandSolder
U3: BMP581; QFN10_BMP581_BOS
U4: BNO085; IC_BNO085; PARTREV v1.17
Y2: Crystal; Crystal_SMD_0603-2Pin_6.0x3.5mm_HandSoldering

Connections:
/Headers/+3V3: C20.1, C21.1, C22.1, C23.1, R13.1, R14.1, R15.2, U3.1 (VDDIO), U3.6 (CSB), U3.10 (VDD), U4.3 (VDD), U4.28 (VDDIO); also elsewhere on the board
/Microcontroller/12C1_SCL: U3.2 (SCK), U4.19 (H_SCL/SCK/RX); also elsewhere on the board
/Microcontroller/12C1_SDA: U3.4 (SDI), U4.20 (H_SDA/H_MISO/TX); also elsewhere on the board
/Microcontroller/BARO_INT: U3.7 (INT); also elsewhere on the board
/Microcontroller/IMU_INT: U4.14 (~H_INT); also elsewhere on the board
/Microcontroller/IMU_RST: U4.11 (~RST); also elsewhere on the board
GND: C20.2, C21.2, C22.2, C23.2, C24.1, C25.2, C26.2, U3.3 (VSS), U3.5 (SDO), U3.8 (VSS), U3.9 (VSS), U4.2 (GND), U4.5 (PS1), U4.6 (PS0/WAKE), U4.10 (CLKSEL0), U4.17 (SA0/H_MOSI), U4.25 (GNDIO); also elsewhere on the board
unnamed: C24.2, U4.9 (CAP)
unnamed: R14.2, U4.15 (ENV_SCL)
unnamed: R13.2, U4.16 (ENV_SDA)
unnamed: C26.1, U4.27 (XIN32), Y2.2
unnamed: C25.1, U4.26 (XOUT32/CLKSEL1), Y2.1
unnamed: R15.1, U4.4 (~BOOT)

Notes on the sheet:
CAS Board 2025
Inertial Measurement Unit
Pressure Sensor

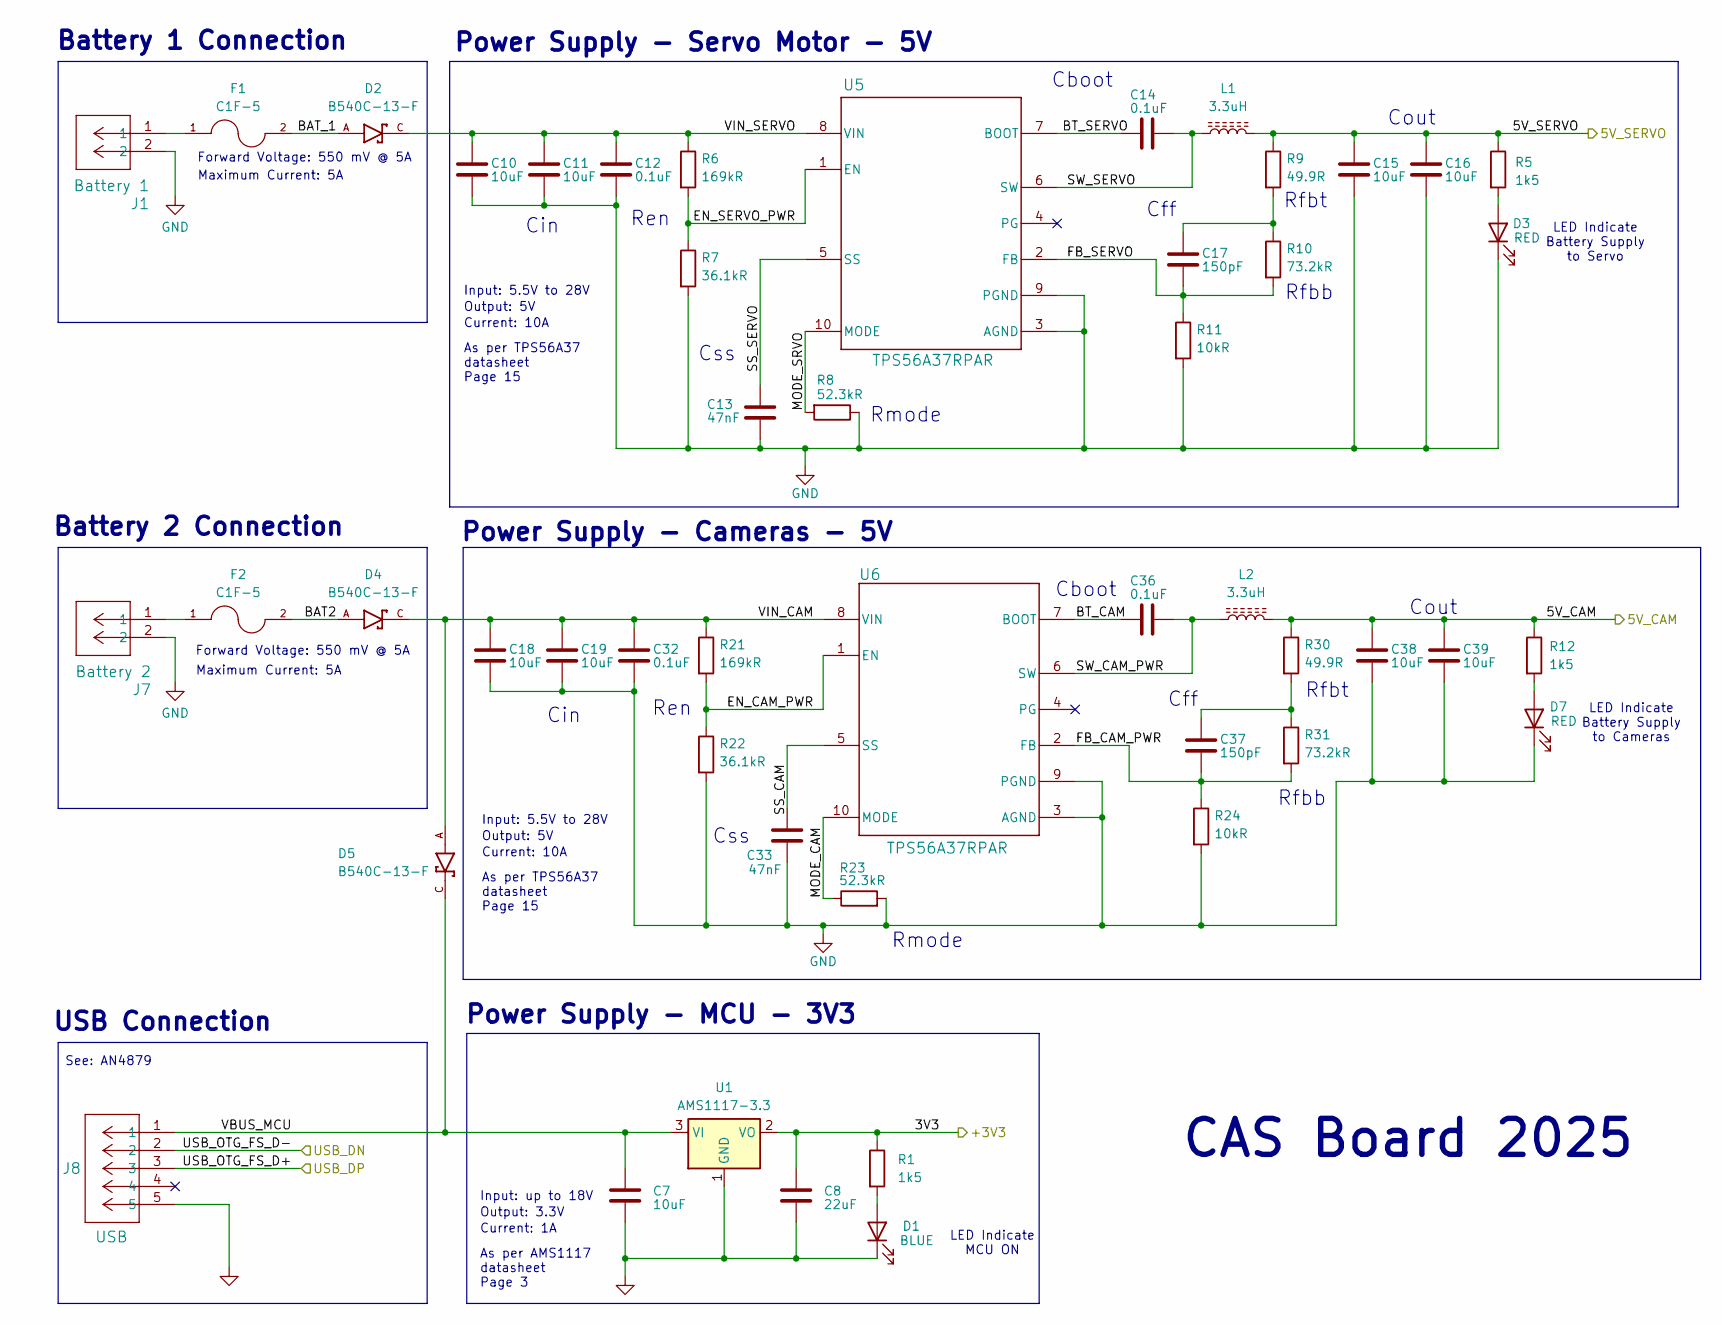
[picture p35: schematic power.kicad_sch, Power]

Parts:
C7, C10, C11, C15, C16, C18, C19, C38, C39: 10uF; C_0805_2012Metric
C8: 22uF; C_0805_2012Metric
C12, C14, C32, C36: 0.1uF; C_0805_2012Metric
C13, C33: 47nF; C_0805_2012Metric
C17, C37: 150pF; C_0805_2012Metric
D1: BLUE; LED_0805_2012Metric
D2, D4, D5: B540C-13-F; DIOM6959X245N; PARTREV V1.0
D3, D7: RED; LED_0805_2012Metric
F1, F2: C1F-5; FUSC3215X83N; PARTREV Jan2019
J1: Battery 1; CONN_SD-5566-002_02_MOL
J7: Battery 2; CONN_SD-5566-002_02_MOL
J8: USB; CON00317_5_MOL
L1, L2: 3.3uH; L_0805_2012Metric_Pad1.05x1.20mm_HandSolder
R1, R5: 1k5; C_0805_2012Metric
R6, R21: 169kR; C_0805_2012Metric
R7, R22: 36.1kR; C_0805_2012Metric
R8, R23: 52.3kR; C_0805_2012Metric
R9, R30: 49.9R; C_0805_2012Metric
R10, R31: 73.2kR; C_0805_2012Metric
R11, R24: 10kR; C_0805_2012Metric
R12: 1k5; R_0805_2012Metric_Pad1.20x1.40mm_HandSolder
U1: AMS1117-3.3; SOT-223-3_TabPin2
U5, U6: TPS56A37RPAR; RPA0010A-MFG

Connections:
/Microcontroller/USB_OTG_FS_D+: J8.3; also elsewhere on the board
/Microcontroller/USB_OTG_FS_D-: J8.2; also elsewhere on the board
/Power/3V3: C8.1, R1.1, U1.2 (VO); also elsewhere on the board
/Power/5V_CAM: C38.1, C39.1, L2.2, R12.1, R30.1; also elsewhere on the board
/Power/5V_SERVO: C15.1, C16.1, L1.2, R5.1, R9.1; also elsewhere on the board
/Power/BAT2: D4.A, F2.2
/Power/BAT_1: D2.A, F1.2
/Power/BT_CAM: C36.1, U6.7 (BOOT)
/Power/BT_SERVO: C14.1, U5.7 (BOOT)
/Power/EN_CAM_PWR: R21.2, R22.1, U6.1 (EN)
/Power/EN_SERVO_PWR: R6.2, R7.1, U5.1 (EN)
/Power/FB_CAM_PWR: C37.2, R24.1, R31.2, U6.2 (FB)
/Power/FB_SERVO: C17.2, R10.2, R11.1, U5.2 (FB)
/Power/MODE_CAM: R23.1, U6.10 (MODE)
/Power/MODE_SRVO: R8.2, U5.10 (MODE)
/Power/SS_CAM: C33.1, U6.5 (SS)
/Power/SS_SERVO: C13.1, U5.5 (SS)
/Power/SW_CAM_PWR: C36.2, L2.1, U6.6 (SW)
/Power/SW_SERVO: C14.2, L1.1, U5.6 (SW)
/Power/VBUS_MCU: C7.1, D5.C, J8.1, U1.3 (VI)
/Power/VIN_CAM: C18.1, C19.1, C32.1, D4.C, D5.A, R21.1, U6.8 (VIN)
/Power/VIN_SERVO: C10.1, C11.1, C12.1, D2.C, R6.1, U5.8 (VIN)
GND: C7.2, C8.2, C10.2, C11.2, C12.2, C13.2, C15.2, C16.2, C18.2, C19.2, C32.2, C33.2, C38.2, C39.2, D1.1 (K), D3.1 (K), D7.1 (K), J1.2, J7.2, J8.5, R7.2, R8.1, R11.2, R22.2, R23.2, R24.2, U1.1 (GND), U5.3 (AGND), U5.9 (PGND), U6.3 (AGND), U6.9 (PGND); also elsewhere on the board
unnamed: C17.1, R9.2, R10.1
unnamed: C37.1, R30.2, R31.1
unnamed: D1.2 (A), R1.2
unnamed: D3.2 (A), R5.2
unnamed: D7.2 (A), R12.2
unnamed: F1.1, J1.1
unnamed: F2.1, J7.1

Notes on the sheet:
Cff
USB Connection
Output: 5V
Current: 10A
Battery 1 Connection
Maximum Current: 5A
LED Indicate MCU ON
Rfbb
See: AN4879
Forward Voltage: 550 mV @ 5A
Output: 3.3V
Cout
Ren
LED Indicate Battery Supply to Cameras
Power Supply - Servo Motor - 5V
Input: 5.5V to 28V
CAS Board 2025
Css
Current: 1A
Cboot
LED Indicate Battery Supply to Servo
As per TPS56A37 datasheet Page 15
Cin
As per AMS1117 datasheet Page 3
Power Supply - MCU - 3V3
Rfbt
Rmode
Input: up to 18V
Battery 2 Connection
Power Supply - Cameras - 5V

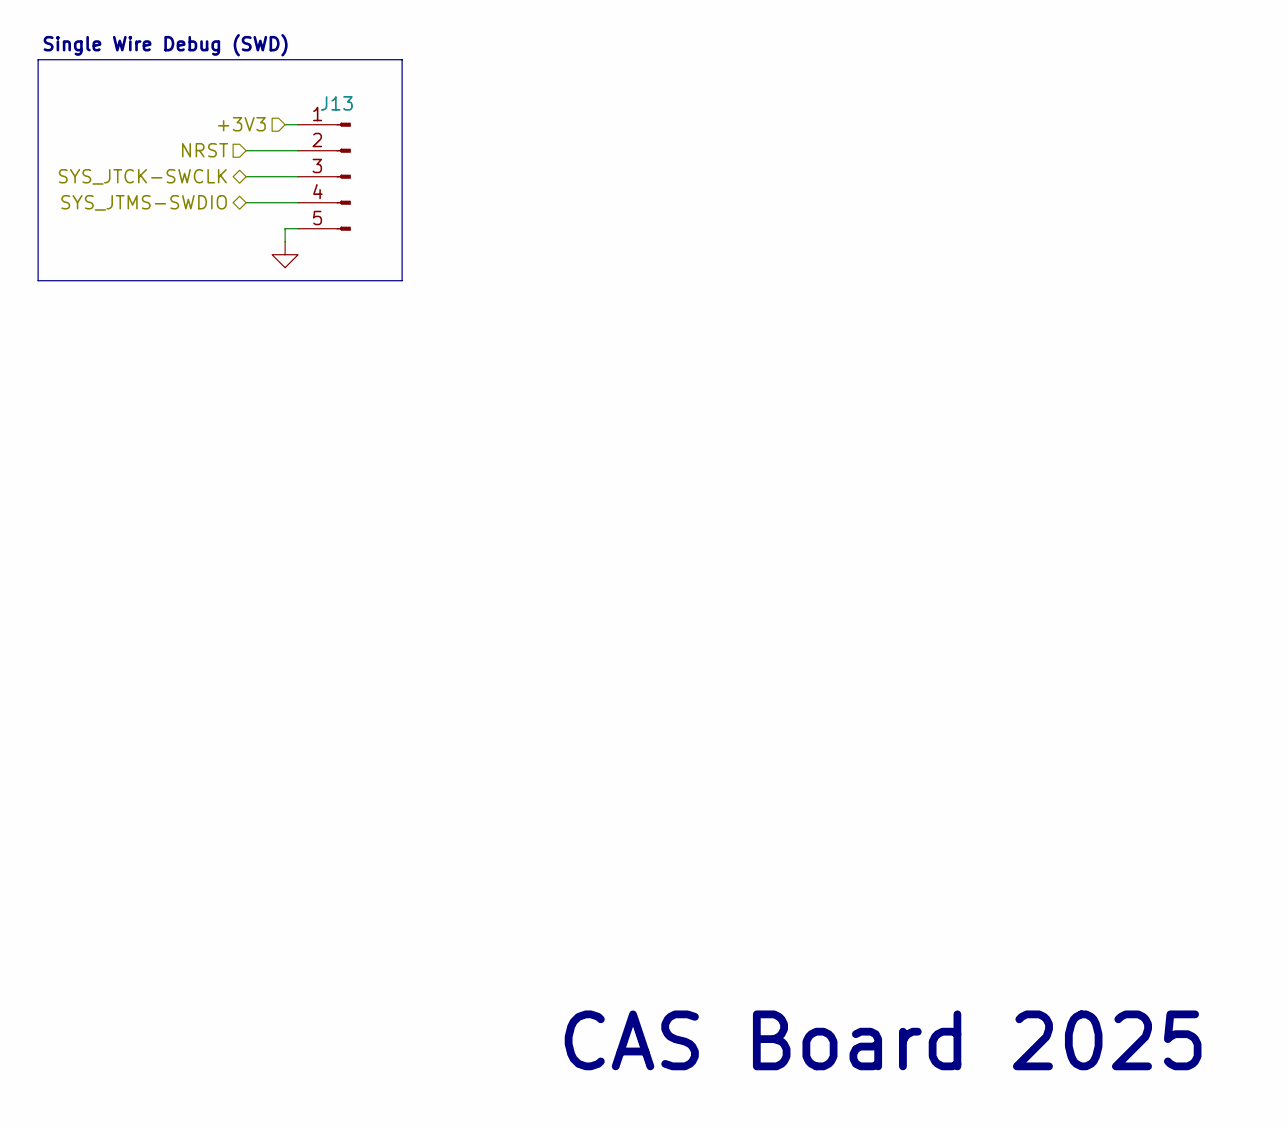
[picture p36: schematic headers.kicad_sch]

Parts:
J13: SWD Header; PinHeader_1x05_P2.54mm_Vertical

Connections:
/Headers/+3V3: J13.1; also elsewhere on the board
/Microcontroller/SYS_JTCK-SWCLK: J13.3; also elsewhere on the board
/Microcontroller/SYS_JTMS-SWDIO: J13.4; also elsewhere on the board
GND: J13.5; also elsewhere on the board
NRST: J13.2; also elsewhere on the board

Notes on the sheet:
CAS Board 2025
Single Wire Debug (SWD)

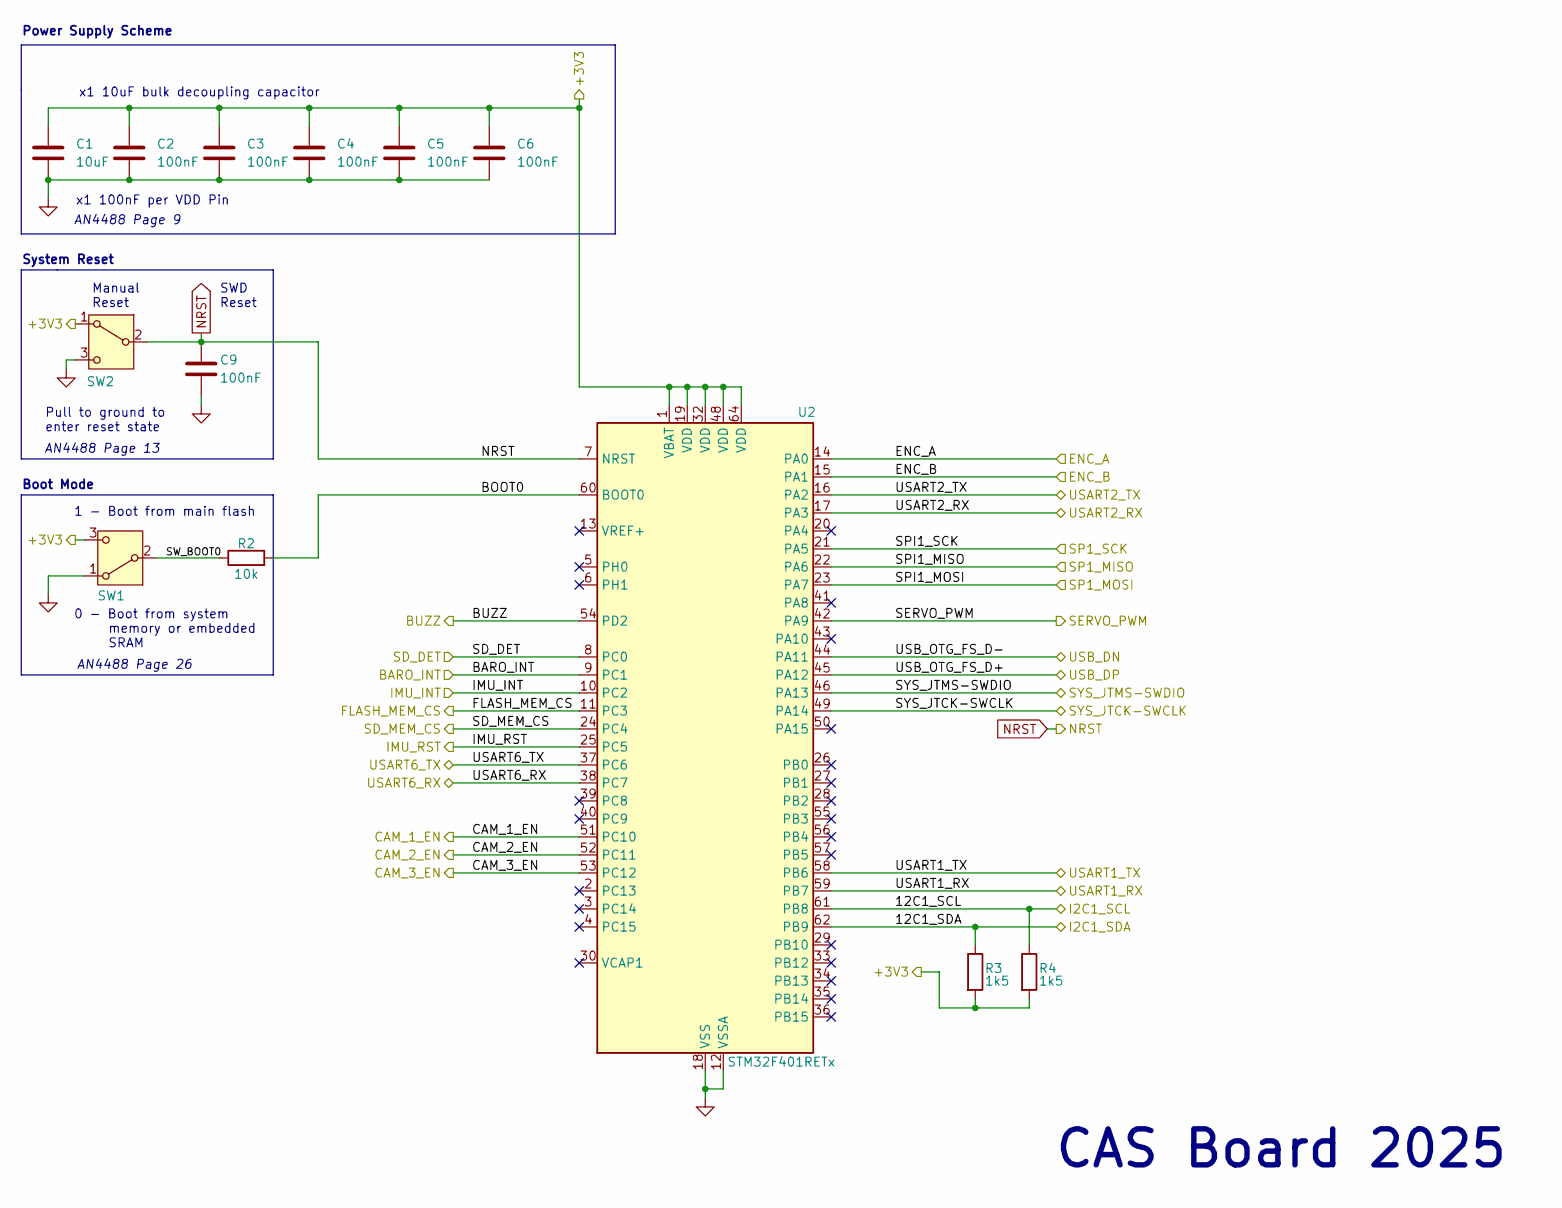
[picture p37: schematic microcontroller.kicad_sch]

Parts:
C1: 10uF; C_0805_2012Metric
C2, C3, C4, C5, C6, C9: 100nF; C_0805_2012Metric
R2: 10k; C_0805_2012Metric
R3, R4: 1k5; C_0805_2012Metric
SW1: Boot Switch; SW_SPDT_PCM12
SW2: System Reset; SW_SPDT_PCM12
U2: STM32F401RETx; LQFP-64_10x10mm_P0.5mm

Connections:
/Headers/+3V3: C1.1, C2.1, C3.1, C4.1, C5.1, C6.1, R3.2, R4.2, SW1.3 (C), SW2.1 (A), U2.1 (VBAT), U2.19 (VDD), U2.32 (VDD), U2.48 (VDD), U2.64 (VDD); also elsewhere on the board
/Microcontroller/12C1_SCL: R4.1, U2.61 (PB8); also elsewhere on the board
/Microcontroller/12C1_SDA: R3.1, U2.62 (PB9); also elsewhere on the board
/Microcontroller/BARO_INT: U2.9 (PC1); also elsewhere on the board
/Microcontroller/BOOT0: R2.2, U2.60 (BOOT0)
/Microcontroller/BUZZ: U2.54 (PD2); also elsewhere on the board
/Microcontroller/CAM_1_EN: U2.51 (PC10); also elsewhere on the board
/Microcontroller/CAM_2_EN: U2.52 (PC11); also elsewhere on the board
/Microcontroller/CAM_3_EN: U2.53 (PC12); also elsewhere on the board
/Microcontroller/ENC_A: U2.14 (PA0); also elsewhere on the board
/Microcontroller/ENC_B: U2.15 (PA1); also elsewhere on the board
/Microcontroller/FLASH_MEM_CS: U2.11 (PC3); also elsewhere on the board
/Microcontroller/IMU_INT: U2.10 (PC2); also elsewhere on the board
/Microcontroller/IMU_RST: U2.25 (PC5); also elsewhere on the board
/Microcontroller/SD_DET: U2.8 (PC0); also elsewhere on the board
/Microcontroller/SD_MEM_CS: U2.24 (PC4); also elsewhere on the board
/Microcontroller/SERVO_PWM: U2.42 (PA9); also elsewhere on the board
/Microcontroller/SPI1_MISO: U2.22 (PA6); also elsewhere on the board
/Microcontroller/SPI1_MOSI: U2.23 (PA7); also elsewhere on the board
/Microcontroller/SPI1_SCK: U2.21 (PA5); also elsewhere on the board
/Microcontroller/SW_BOOT0: R2.1, SW1.2 (B)
/Microcontroller/SYS_JTCK-SWCLK: U2.49 (PA14); also elsewhere on the board
/Microcontroller/SYS_JTMS-SWDIO: U2.46 (PA13); also elsewhere on the board
/Microcontroller/USART1_RX: U2.59 (PB7); also elsewhere on the board
/Microcontroller/USART1_TX: U2.58 (PB6); also elsewhere on the board
/Microcontroller/USART2_RX: U2.17 (PA3); also elsewhere on the board
/Microcontroller/USART2_TX: U2.16 (PA2); also elsewhere on the board
/Microcontroller/USART6_RX: U2.38 (PC7); also elsewhere on the board
/Microcontroller/USART6_TX: U2.37 (PC6); also elsewhere on the board
/Microcontroller/USB_OTG_FS_D+: U2.45 (PA12); also elsewhere on the board
/Microcontroller/USB_OTG_FS_D-: U2.44 (PA11); also elsewhere on the board
GND: C1.2, C2.2, C3.2, C4.2, C5.2, C6.2, C9.2, SW1.1 (A), SW2.3 (C), U2.12 (VSSA), U2.18 (VSS), U2.31 (VSS), U2.47 (VSS), U2.63 (VSS); also elsewhere on the board
NRST: C9.1, SW2.2 (B), U2.7 (NRST); also elsewhere on the board

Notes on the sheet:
1 - Boot from main flash
SWD Reset
x1 100nF per VDD Pin
AN4488 Page 26
CAS Board 2025
0 - Boot from system memory or embedded SRAM
x1 10uF bulk decoupling capacitor
Power Supply Scheme
AN4488 Page 9
Manual Reset
System Reset
AN4488 Page 13
Boot Mode
Pull to ground to enter reset state

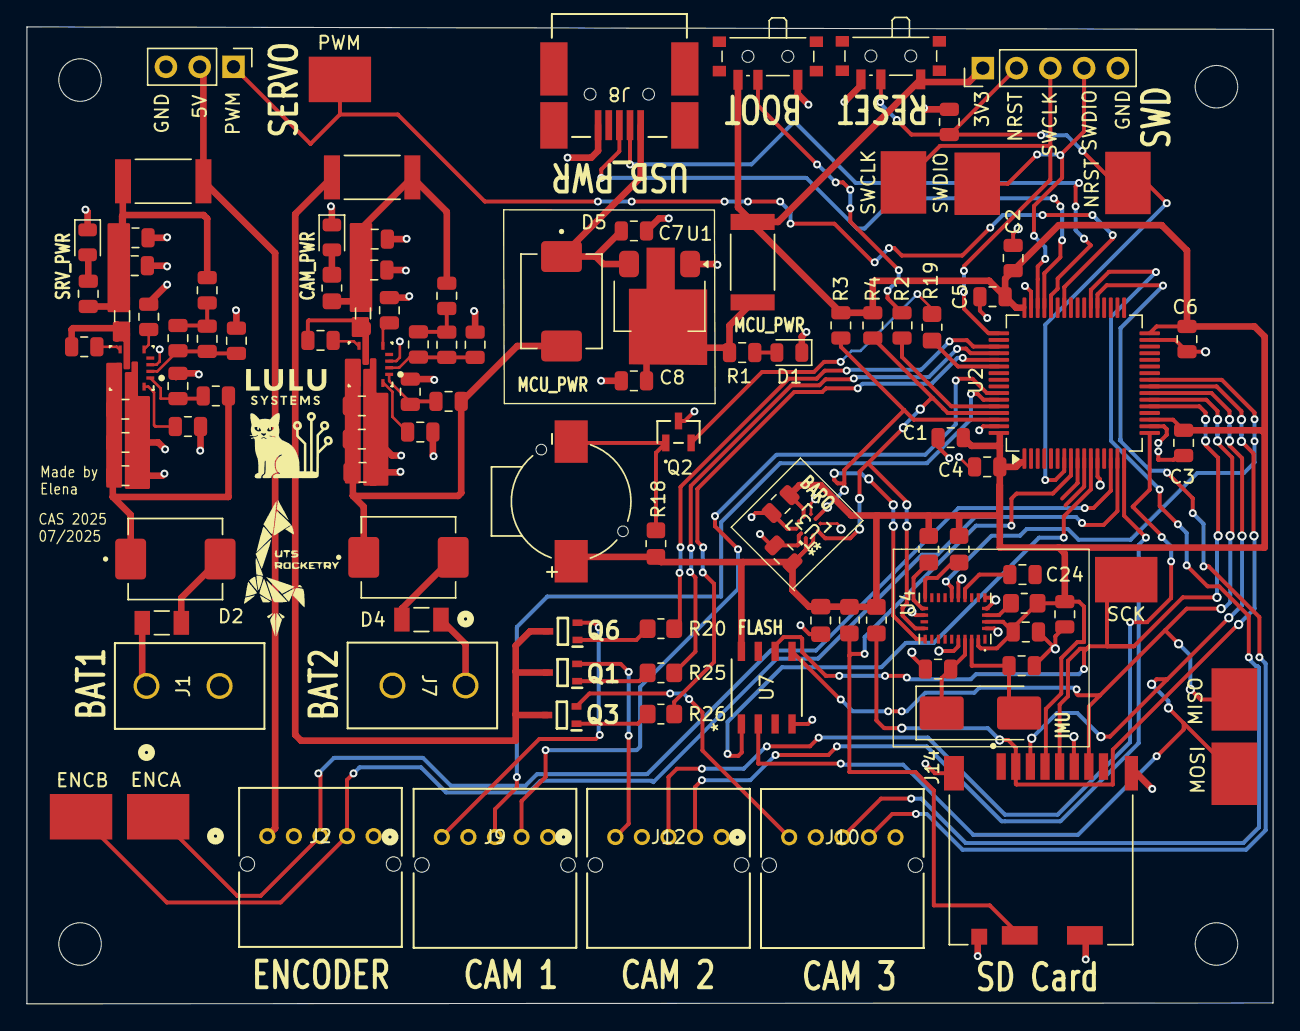
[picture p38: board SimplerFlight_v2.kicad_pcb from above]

Board: 2 copper layers, 93.8 x 73.5 mm, 112 parts (0 on the bottom side), 76 nets.

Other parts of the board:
ENCA: 5016; KEYSTONE_5016
ENCB: 5016; KEYSTONE_5016
MISO: 5016; KEYSTONE_5016
MOSI
: 5016; KEYSTONE_5016
NRST: 5016; KEYSTONE_5016
PWM: 5016; KEYSTONE_5016
SCK: 5016; KEYSTONE_5016
SWCLK: 5016; KEYSTONE_5016
SWDIO: 5016; KEYSTONE_5016

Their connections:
/Microcontroller/ENC_A: ENCA.TP; also elsewhere on the board
/Microcontroller/ENC_B: ENCB.TP; also elsewhere on the board
/Microcontroller/SERVO_PWM: PWM.TP; also elsewhere on the board
/Microcontroller/SPI1_MISO: MISO.TP; also elsewhere on the board
/Microcontroller/SPI1_MOSI: MOSI.TP; also elsewhere on the board
/Microcontroller/SPI1_SCK: SCK.TP; also elsewhere on the board
/Microcontroller/SYS_JTCK-SWCLK: SWCLK.TP; also elsewhere on the board
/Microcontroller/SYS_JTMS-SWDIO: SWDIO.TP; also elsewhere on the board
NRST: NRST.TP; also elsewhere on the board

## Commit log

2025-06-14 Init files
    [629105150521 (rev1).stp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]
2025-06-16 Clean and rename to V2
    [629105150521 (rev1).stp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]
2025-06-16 Add USB Mini B to replace USB Micro
    [675031020.stp, SimplerFlight_v2.kicad_pcb, SimplerFlight_v2.kicad_sch]
2025-06-16 Image folder and edit readme
    [SimplerFlight_v2.kicad_sch]
2025-06-16 Update readme and some silskreen labeles
    [QFN10_BMP581_BOS.step, SimplerFlight_v2.kicad_pcb, SimplerFlight_v2.kicad_sch]
2025-06-16 Fix name
    [SimplerFlight_v2.kicad_pcb, SimplerFlight_v2.kicad_sch]
2025-06-23 Reorganisation and draft of power supply
    [039281023.stp, B540C-13-F.step, BNO085--3DModel-STEP-510211.STEP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]
2025-06-24 Remove redundant diode for camera supply
    [SimplerFlight_v2.kicad_sch, power.kicad_sch]
2025-06-25 Upload architecture diagram, start sensor schematic, add simulation files
    [SimplerFlight_v2.kicad_sch, power.kicad_sch, sensors.kicad_sch]
2025-07-02 addecd stuff
    [SimplerFlight_v2.kicad_sch, microcontroller.kicad_sch, peripherals.kicad_sch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]
2025-07-04 Initiliase main components
    [DM3CS-SF.step, SimplerFlight_v2.kicad_pcb, WIN_SN-8_WIN.step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]
2025-07-05 Update schematic, pending power sims, updated README
    [IRF520NPBF.step, SSOT3_3X1P5_ONS.step, SimplerFlight_v2.kicad_pcb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]
2025-07-07 Remove transistor enable for servo power. Added falstad sim files
    [SimplerFlight_v2.kicad_pcb, microcontroller.kicad_sch, peripherals.kicad_sch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]
2025-07-07 Updated schematics
    [SimplerFlight_v2.kicad_pcb, SimplerFlight_v2.kicad_sch, microcontroller.kicad_sch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]
2025-07-07 added schotkey diode for encoder power
    [peripherals.kicad_sch]
2025-07-07 Update buzzer circuit and add simulation
    [PS1240P02BT.step, peripherals.kicad_sch]
2025-07-07 remove schotkey diodes from servo and encoder interfaces
    [peripherals.kicad_sch]
2025-07-07 Add camera power sim and made gitignore file
2025-07-07 Modify README to point to correct transistor used for camera
2025-07-07 Redo footprints and add mosfet for camera power control
    [BSS816NWH6327XTSA1.stp, SimplerFlight_v2.kicad_pcb, peripherals.kicad_sch]
2025-07-07 Update simulation for buzzer NPN transistor to use correct hFE value
    [SimplerFlight_v2.kicad_pcb]
2025-07-07 use another shotkey diode for battery to usb intersection for mcu power
    [SimplerFlight_v2.kicad_pcb, power.kicad_sch]
2025-07-07 Use different flash chip with nicer documentation
    [SOP8_150_MAC.step, SimplerFlight_v2.kicad_pcb, storage.kicad_sch]
2025-07-07 labels for storage schematic
    [storage.kicad_sch]
2025-07-07 Add net names to power
    [power.kicad_sch]
2025-07-07 Use heirarchical labels
    [SimplerFlight_v2.kicad_sch, microcontroller.kicad_sch, peripherals.kicad_sch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]
2025-07-08 Broke headers into own heiarchicial sheet
    [headers.kicad_sch, microcontroller.kicad_sch, peripherals.kicad_sch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]
2025-07-08 Added voltage/signal test points
    [5016.step, CSRN2512FKR500.step, SimplerFlight_v2.kicad_pcb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]
2025-07-08 Removed external highspeed clock
    [headers.kicad_sch, microcontroller.kicad_sch]
2025-07-08 Initial layout for PCB components, updated README with images. Removed some test points and headers from final layout. Pending addition of buzzer. Pending additional power testing and pending routing.
    [SimplerFlight_v2.kicad_pcb, SimplerFlight_v2.kicad_sch, headers.kicad_sch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]
2025-07-08 Update images to show updated schematics using hierarchical pins for power lines
2025-07-13 Redo layout and redoing buck converters
    [CBT-09427-SMT.step, RPA0010A.stp, SimplerFlight_v2.kicad_pcb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]
2025-07-13 Udpate power schematic
    [power.kicad_sch]
2025-07-14 Update screenshots and addeed 3D files
    [SimplerFlight_v2.kicad_pcb]
2025-07-14 Removed uncvessary test points and headerrs. Added missing values. Update images of schematics
    [SimplerFlight_v2.kicad_sch, headers.kicad_sch, sensors.kicad_sch]
2025-07-16 Routing for cam buck converter
    [SimplerFlight_v2.kicad_pcb, SimplerFlight_v2.kicad_sch, headers.kicad_sch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]
2025-07-16 Routes for power
    [SimplerFlight_v2.kicad_pcb]
2025-07-16 More routing - sync
    [SimplerFlight_v2.kicad_pcb]
2025-07-16 Re-arranged sensor, storage and peripheral component layout
    [SimplerFlight_v2.kicad_pcb]
2025-07-16 more routing
    [SimplerFlight_v2.kicad_pcb]
2025-07-21 Finish all essential routing
    [SimplerFlight_v2.kicad_pcb]
